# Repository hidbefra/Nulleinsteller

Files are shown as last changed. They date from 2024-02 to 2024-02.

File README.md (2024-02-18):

Ein Nulleinsteller wird benutzt, um die Werkzeuglänge auf einer CNC-Maschine zu messen.
HI10001136_B.pdf Zeigt die Zusammenstellung. Konstruktion wurde noch nie gebaut und kann fehlerhaft sein

A zero adjuster is used to measure tool length on a CNC machine.
HI10001136_B.pdf Shows the compilation. Construction has never been built and may be defective

BOM HI10001136_B Nulleinsteller
|Pos.|Anz.|Datei Name|Name|
|-----|-----|---|---|
|1|1|HI10001131_A|BCXT53 mitutoyo 123160.0801
|2|1|HI10001133_A|Büchse
|3|1|HI10001134_B|Gehäuse
|4|1|HI10001135_B|Stössel
|5|1|HI10001137_A|Compression Spring-57_6_5-Durovis
|6|1|BN 818 1287230 retaining ring for shafts 14x1_Spring steel|BN 818 1287230 retaining ring for shafts 14x1
|7|1|BN 24 1025643 hexagon socket set screw M5x8_Steel 45 H|BN 24 1025643 hexagon socket set screw M5x8
|8|1|BN 874 1323873 spiral spring pin 4x16_Steel hardened to 420-545 HV|BN 874 1323873 spiral spring pin 4x16

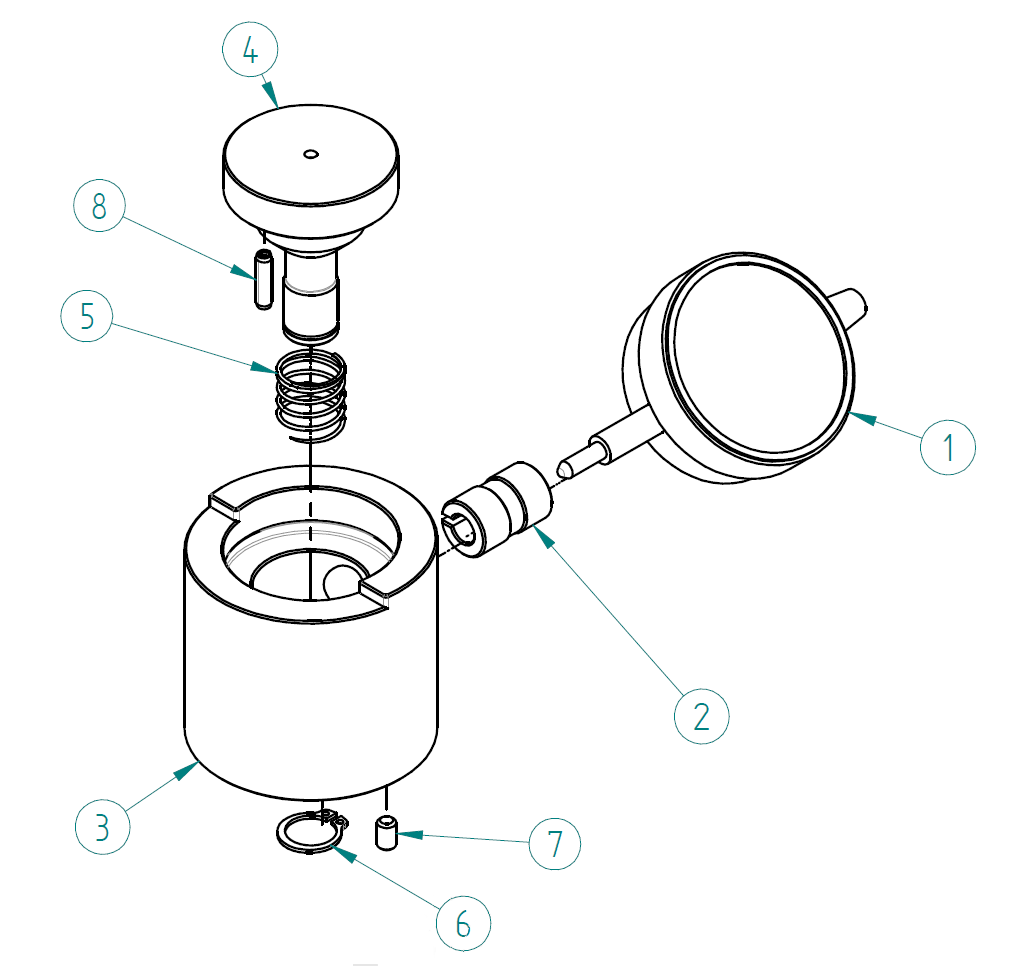
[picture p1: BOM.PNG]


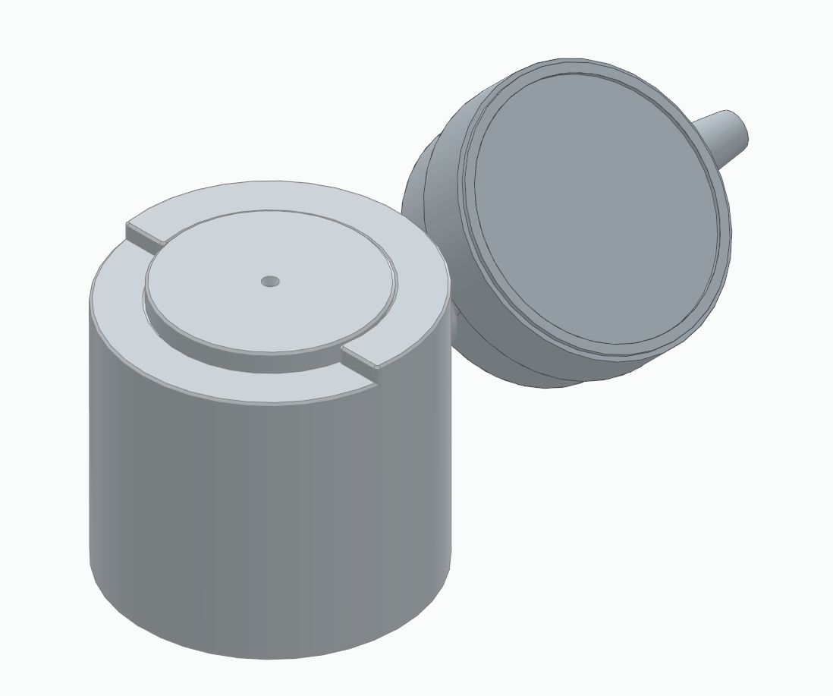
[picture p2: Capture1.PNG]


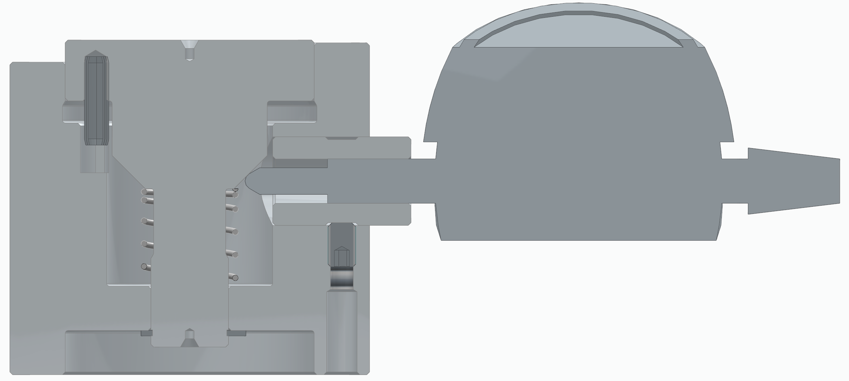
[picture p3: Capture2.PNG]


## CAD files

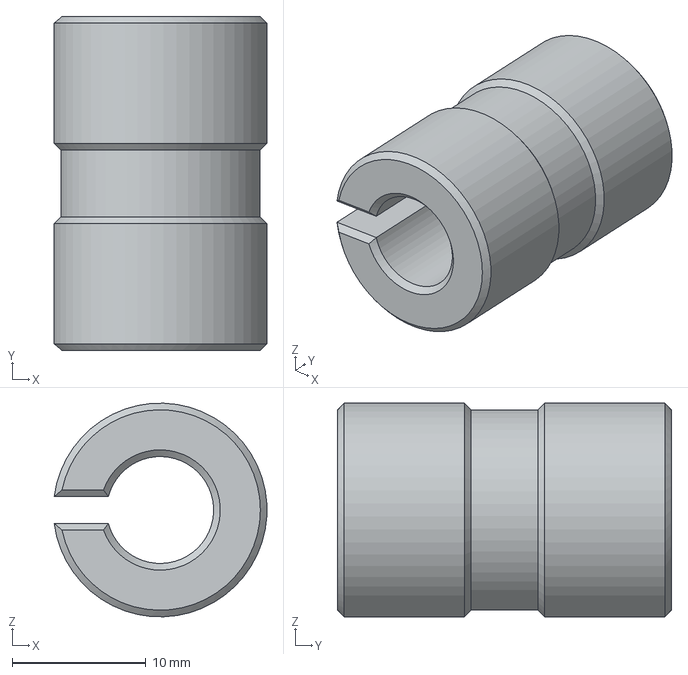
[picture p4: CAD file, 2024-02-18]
HI10001133_A.stp
15.9 x 25.0 x 16.0 mm

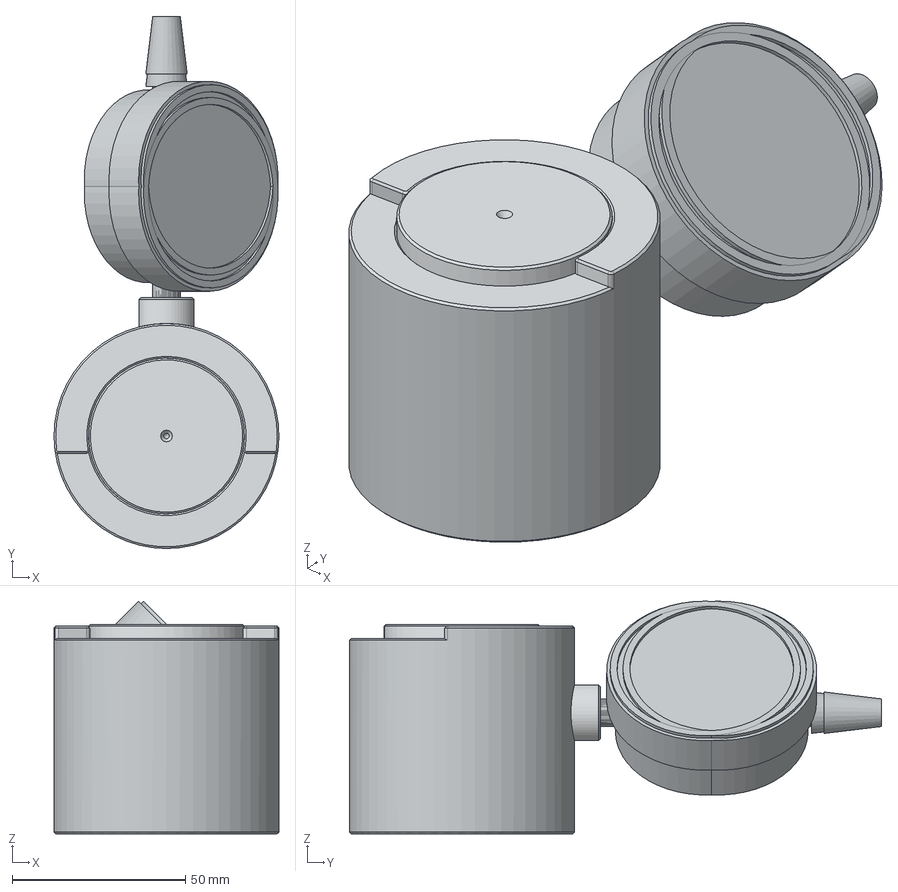
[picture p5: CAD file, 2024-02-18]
HI10001136_B.stp
65.0 x 153.7 x 67.2 mm
HI10001132_A
HI10001131_A x 2
HI10001133_A
HI10001134_B
HI10001135_B x 2
BN 874 1323873 spiral spring pin 4x16_Steel hardened to 420-545 HV x 2
HI10001137_A
BN 818 1287230 retaining ring for shafts 14x1_Spring steel
BN 24 1025643 hexagon socket set screw M5x8_Steel 45 H

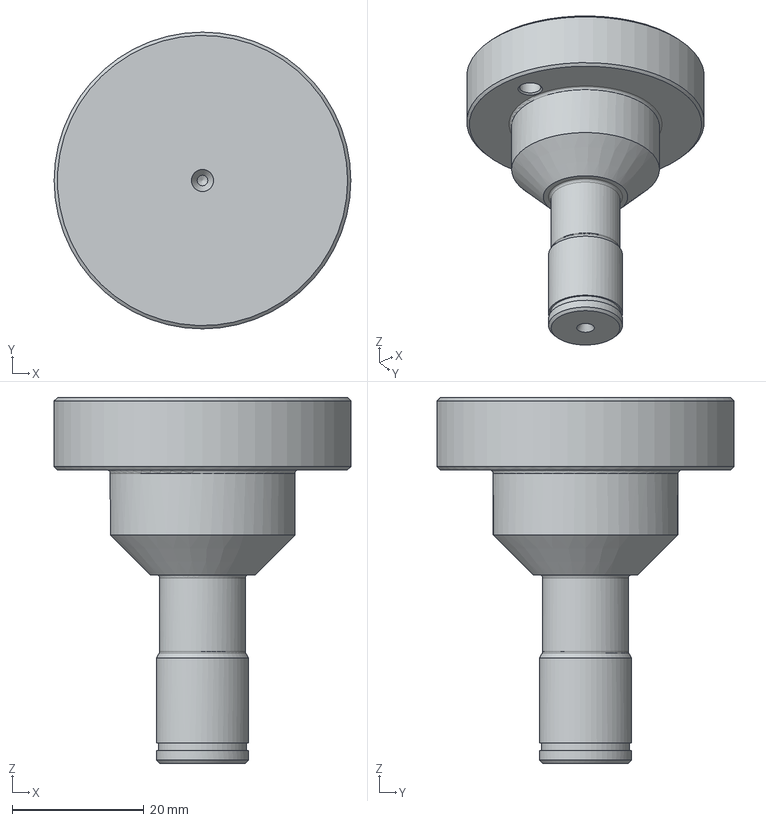
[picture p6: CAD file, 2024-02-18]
HI10001135_B.stp
45.0 x 45.0 x 55.5 mm

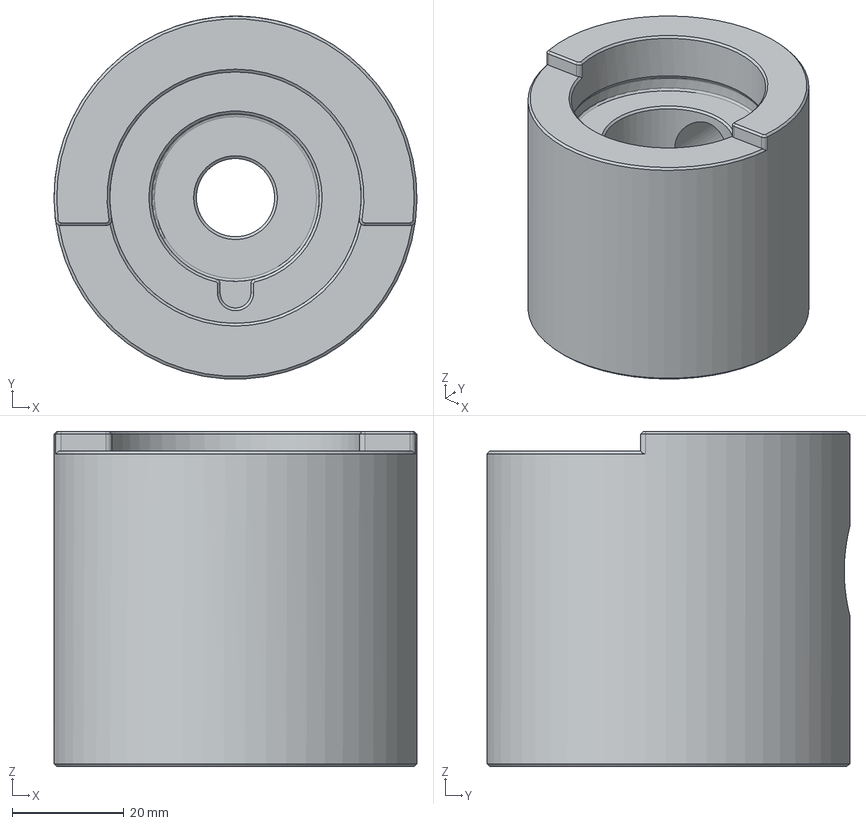
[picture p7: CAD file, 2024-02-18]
HI10001134_B.stp
65.0 x 65.0 x 60.0 mm

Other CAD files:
HI10001133_A.dxf
HI10001134_B.dxf
HI10001135_B.dxf
HI10001136_B.dxf

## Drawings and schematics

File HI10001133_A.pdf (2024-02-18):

1:1

A

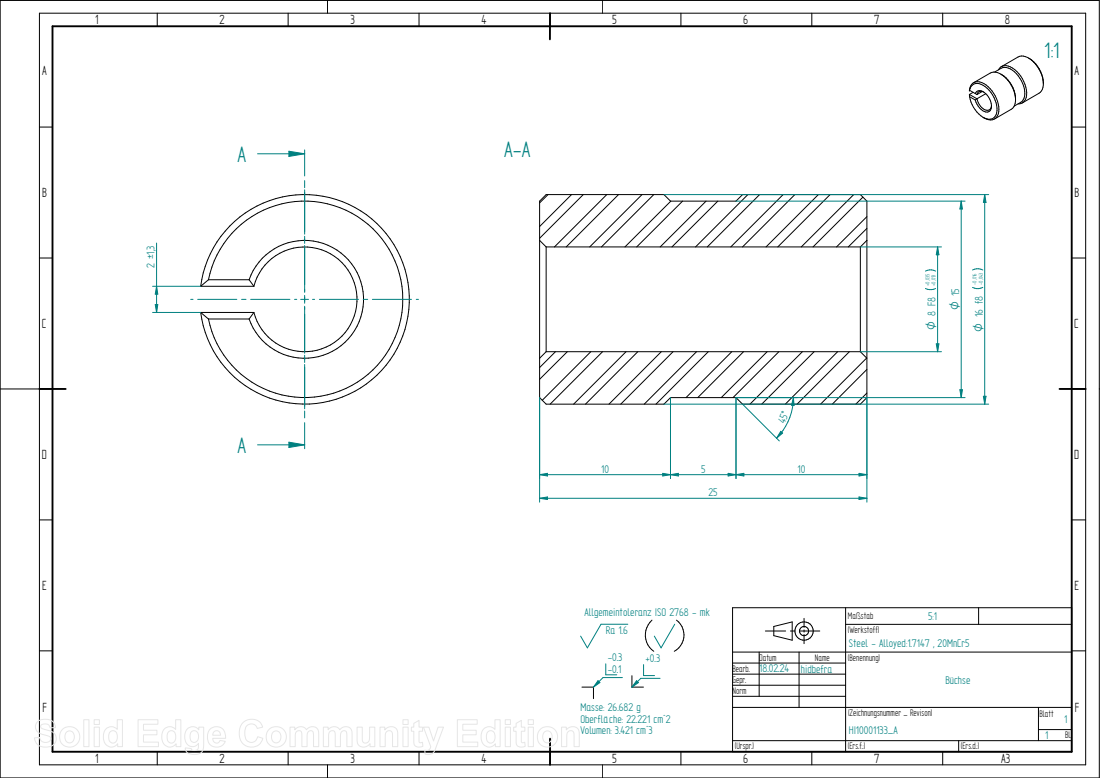
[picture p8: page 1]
Maßstab; Blatt; (Zeichnungsnummer _ Revison); (Werkstoff); (Urspr.); (Ers.f.:); (Ers.d.:); Steel - Alloyed:1.7147 , 20MnCr5; Masse: 26.682 g Oberfläche: 22.221 cm^2 Volumen: 3.421 cm^3

Allgemeintoleranz ISO 2768 - mk

Datum | Name | (Benennung) Büchse
Bearb. | 18.02.24 | hidbefra
Gepr.
Norm

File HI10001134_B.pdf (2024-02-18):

1:1

A-A

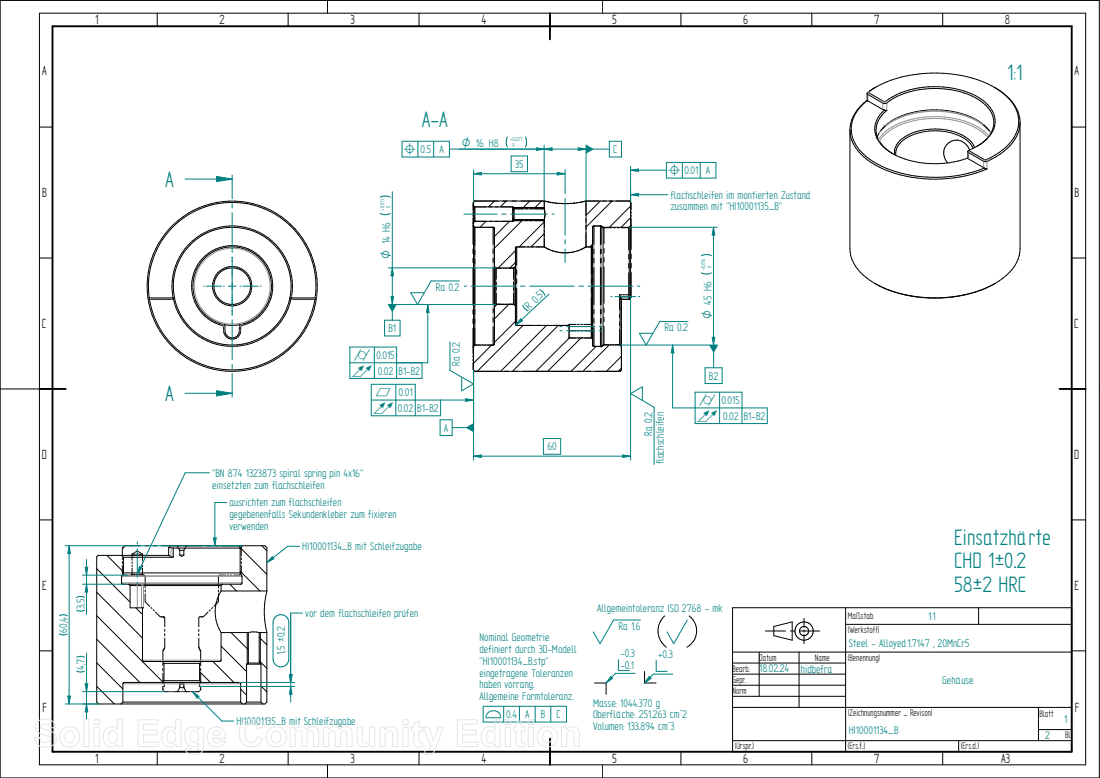
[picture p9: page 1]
Maßstab; Blatt; (Zeichnungsnummer _ Revison); (Werkstoff); (Urspr.); (Ers.f.:); (Ers.d.:); Steel - Alloyed:1.7147 , 20MnCr5; Masse: 1044.370 g Oberfläche: 251.263 cm^2 Volumen: 133.894 cm^3; HI10001134_B mit Schleifzugabe; HI10001135_B mit Schleifzugabe; Einsatzhärte CHD 1u0.2 58u2 HRC; Ra 0.2 flachschleifen

flachschleifen im montierten Zustand
zusammen mit "HI10001135_B"

j | 0.015
_ | 0.02 | B1-B2
r | 0.01

"BN 874 1323873 spiral spring pin 4x16"
einsetzten zum flachschleifen
ausrichten zum flachschleifen
gegebenenfalls Sekundenkleber zum fixieren
verwenden

Allgemeintoleranz ISO 2768 - mk

vor dem flachschleifen prüfen

Nominal Geometrie
definiert durch 3D-Modell
"HI10001134_B.stp"
eingetragene Toleranzen
haben vorrang.
Allgemeine Formtoleranz.

Datum | Name | (Benennung) Gehäuse
Bearb. | 18.02.24 | hidbefra
Gepr.
Norm

1:1

A

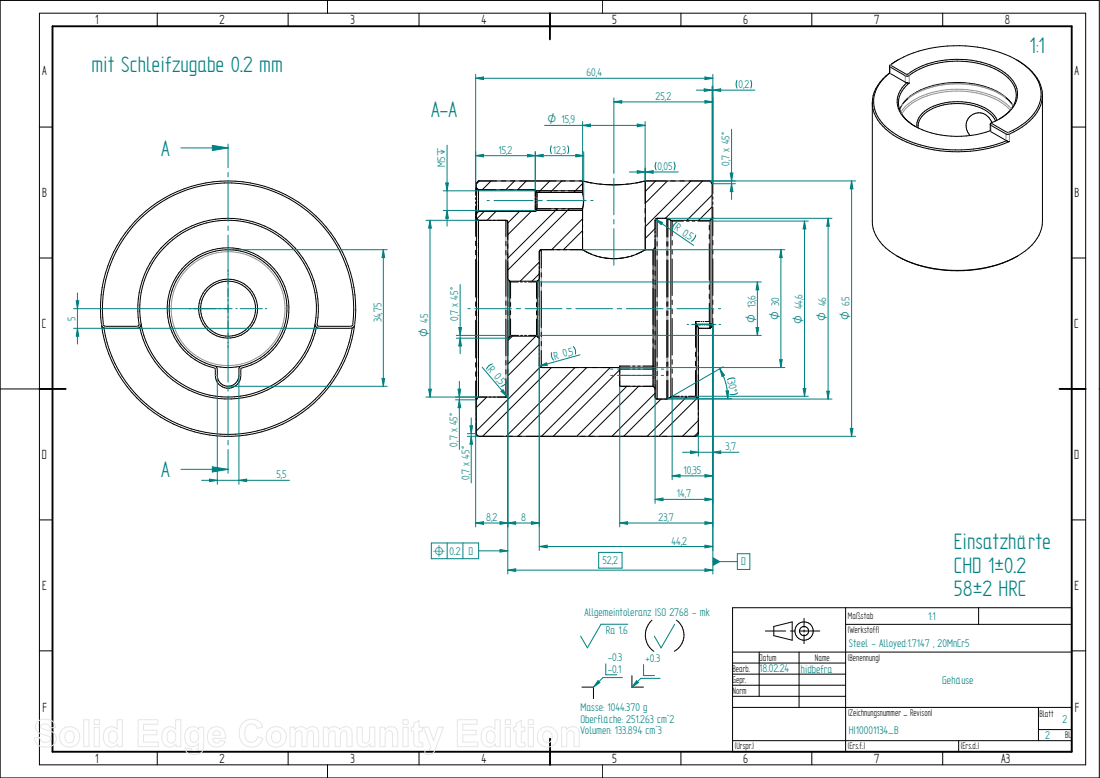
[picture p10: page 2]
Maßstab; Blatt; (Zeichnungsnummer _ Revison); (Werkstoff); (Urspr.); (Ers.f.:); (Ers.d.:); Steel - Alloyed:1.7147 , 20MnCr5; Masse: 1044.370 g Oberfläche: 251.263 cm^2 Volumen: 133.894 cm^3; mit Schleifzugabe 0.2 mm; Einsatzhärte CHD 1u0.2 58u2 HRC

Allgemeintoleranz ISO 2768 - mk

Datum | Name | (Benennung) Gehäuse
Bearb. | 18.02.24 | hidbefra
Gepr.
Norm

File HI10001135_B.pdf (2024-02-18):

1:1

A

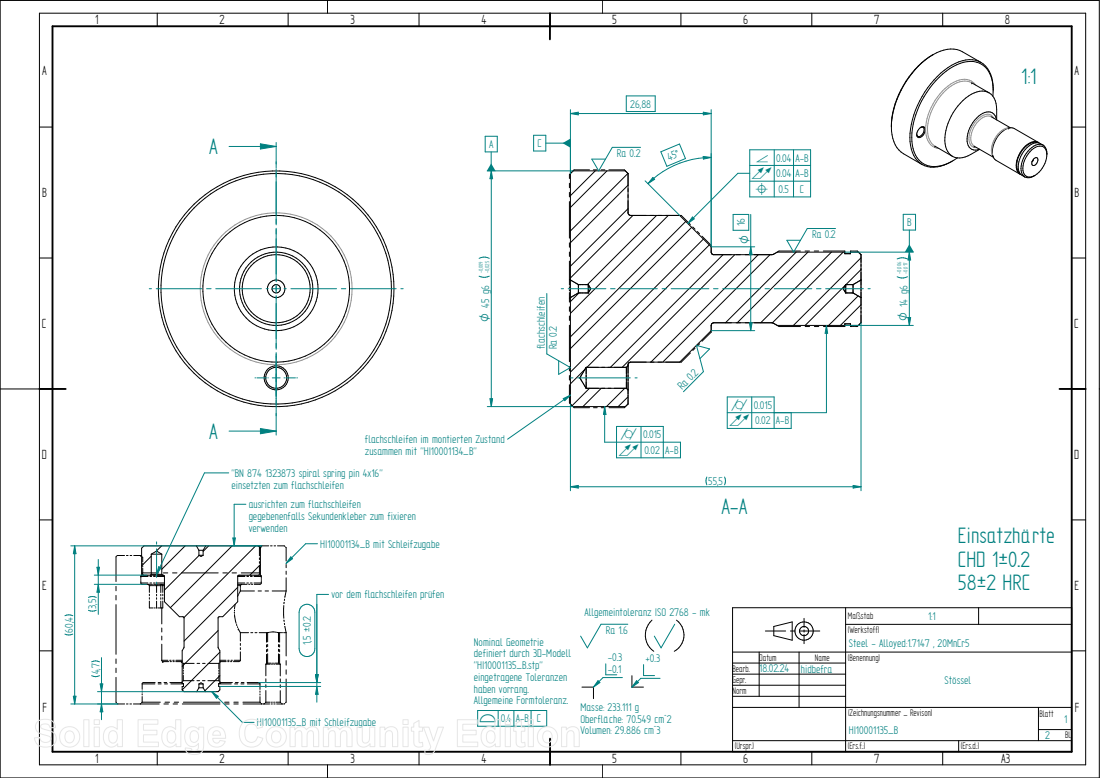
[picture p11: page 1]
Maßstab; (Werkstoff); (Urspr.); (Ers.f.:); (Ers.d.:); Steel - Alloyed:1.7147 , 20MnCr5; Masse: 233.111 g Oberfläche: 70.549 cm^2 Volumen: 29.886 cm^3; flachschleifen; HI10001134_B mit Schleifzugabe; HI10001135_B mit Schleifzugabe; Einsatzhärte CHD 1u0.2 58u2 HRC

g | 0.04 | A-B
_ | 0.04 | A-B
l | 0.5 | C

j | 0.015
_ | 0.02 | A-B

flachschleifen im montierten Zustand
zusammen mit "HI10001134_B"

"BN 874 1323873 spiral spring pin 4x16"
einsetzten zum flachschleifen
ausrichten zum flachschleifen
gegebenenfalls Sekundenkleber zum fixieren
verwenden

vor dem flachschleifen prüfen

Allgemeintoleranz ISO 2768 - mk

Nominal Geometrie
definiert durch 3D-Modell
"HI10001135_B.stp"
eingetragene Toleranzen
haben vorrang.
Allgemeine Formtoleranz.

Datum | Name | (Benennung) Stössel
Bearb. | 18.02.24 | hidbefra
Gepr.
Norm

(Zeichnungsnummer _ Revison) HI10001135_B | Blatt 1

1:1

A

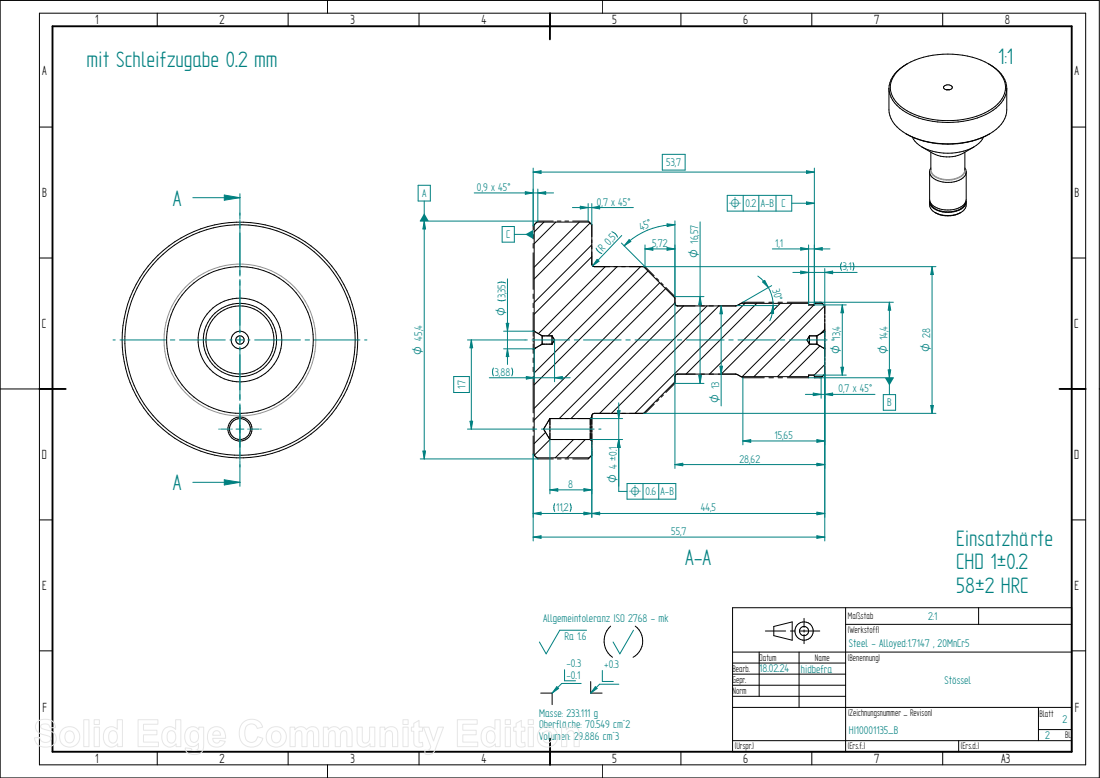
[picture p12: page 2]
Maßstab; Blatt; (Zeichnungsnummer _ Revison); (Werkstoff); (Urspr.); (Ers.f.:); (Ers.d.:); Steel - Alloyed:1.7147 , 20MnCr5; Masse: 233.111 g Oberfläche: 70.549 cm^2 Volumen: 29.886 cm^3; Einsatzhärte CHD 1u0.2 58u2 HRC

mit Schleifzugabe 0.2 mm

Allgemeintoleranz ISO 2768 - mk

Datum | Name | (Benennung) Stössel
Bearb. | 18.02.24 | hidbefra
Gepr.
Norm

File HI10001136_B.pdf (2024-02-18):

1:2

A-A

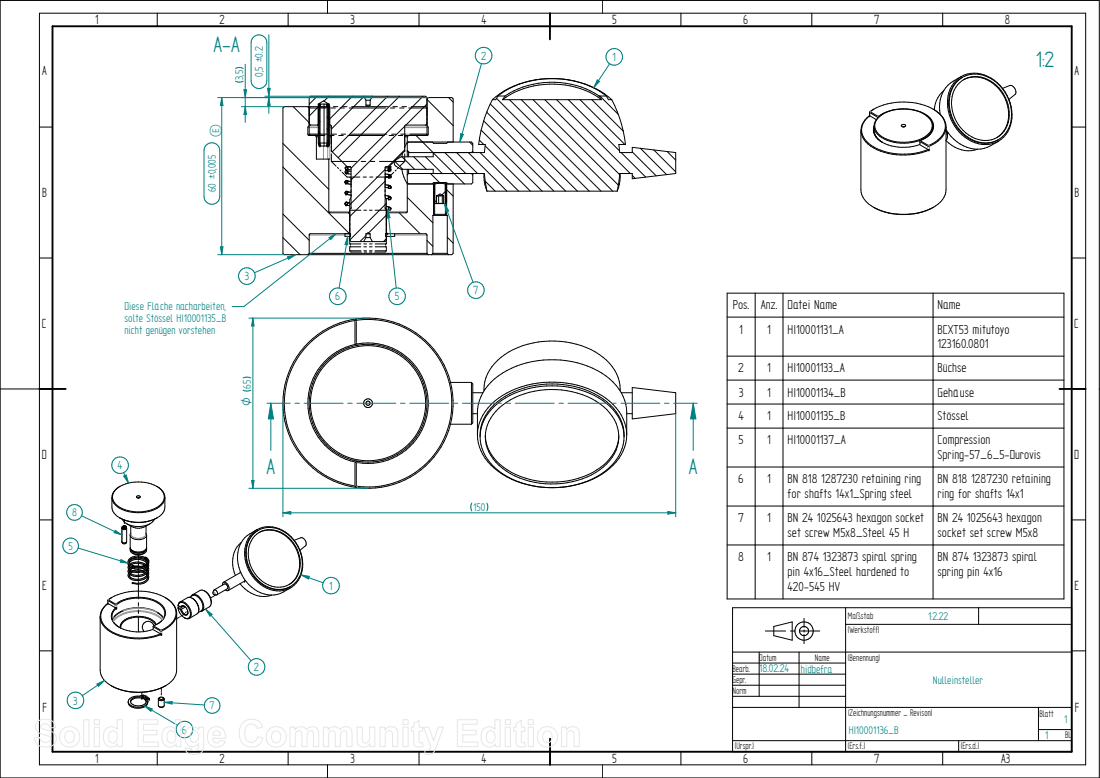
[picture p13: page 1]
Maßstab; Blatt; (Zeichnungsnummer _ Revison); (Werkstoff); (Urspr.); (Ers.f.:); (Ers.d.:); Pos.; Anz.; Datei Name; Name

Diese Fläche nacharbeiten,
solte Stössel HI10001135_B
nicht genügen vorstehen

1 | 1 | HI10001131_A | BCXT53 mitutoyo 123160.0801

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

Datum | Name | (Benennung) Nulleinsteller
Bearb. | 18.02.24 | hidbefra
Gepr.
Norm
